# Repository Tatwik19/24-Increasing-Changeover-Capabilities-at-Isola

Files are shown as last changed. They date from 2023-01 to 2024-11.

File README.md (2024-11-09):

# 24-Increasing-Changeover-Capabilities-at-Isola
Innovation showcase poster pptx

<br />

https://github.com/user-attachments/assets/ee0afaa7-376b-4424-b353-ba5e18c106c2

<br />

The Isola Group is a global company that services the manufacturing industry by producing and supplying a range of products and raw materials. Their Chandler plant is designed specifically to produce copper-fiberglass laminate for PCBs, with a focus on high-speed turnaround low-volume custom substrate. Isola has identified the current copper foil roll changeover solution on their assembly line as a bottleneck. It is currently a slow, partially manual process, and speeding up this portion of the assembly line would allow them to take on more next-day clients, fill more orders, and generate more value. Team 24 has been tasked with designing a solution that can decrease the copper foil changeover time and remove the bottleneck in their line. The deliverables consist of a detailed mechanical and electrical design, a bill of materials (BOM) of the completed solution, and a budget for a completed solution. The solution’s scope is limited to the beginning of the process at the copper foil pallet staged at the machine and ending with loading the copper foil rolls onto the existing chucks.

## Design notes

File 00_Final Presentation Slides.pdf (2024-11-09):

# Final Presentation Team 24

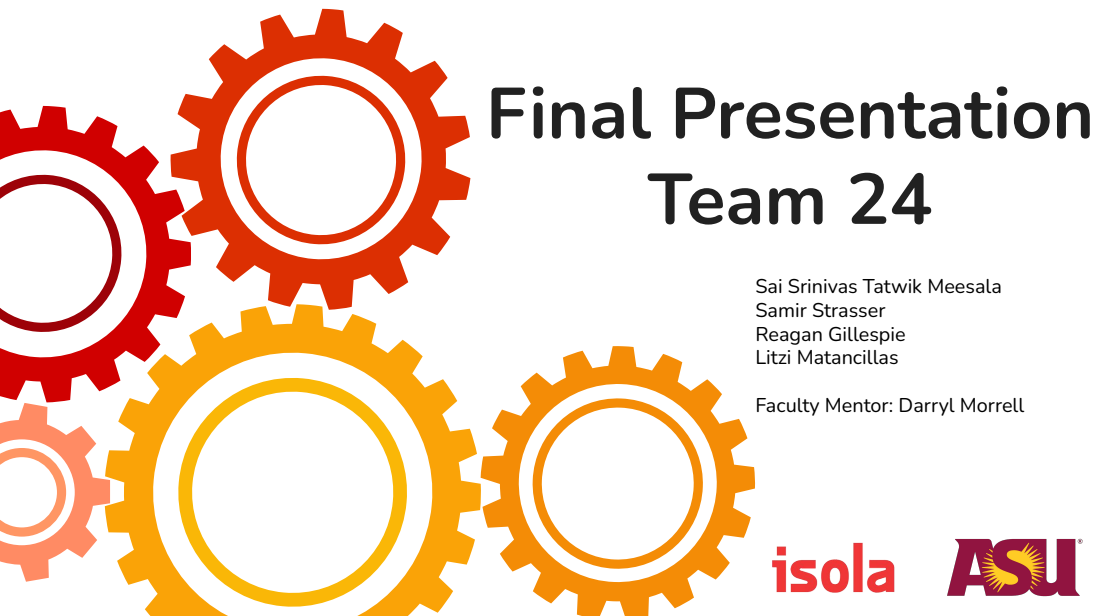
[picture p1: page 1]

Sai Srinivas Tatwik Meesala
Samir Strasser
Reagan Gillespie
Litzi Matancillas
Faculty Mentor: Darryl Morrell

# Problem Statement

## Isola's current copper foil roll changeover solution is largely a

manual process and takes 2 min which is far longer than it should,

## decreasing their ability to fill out next-day Printed Circuit Board

(PCB) orders. Along with that it currently can only hold 2 rolls,

## because of this it has become a bottleneck in the PCB material

production line.

# Concept: Dual Head Lifter

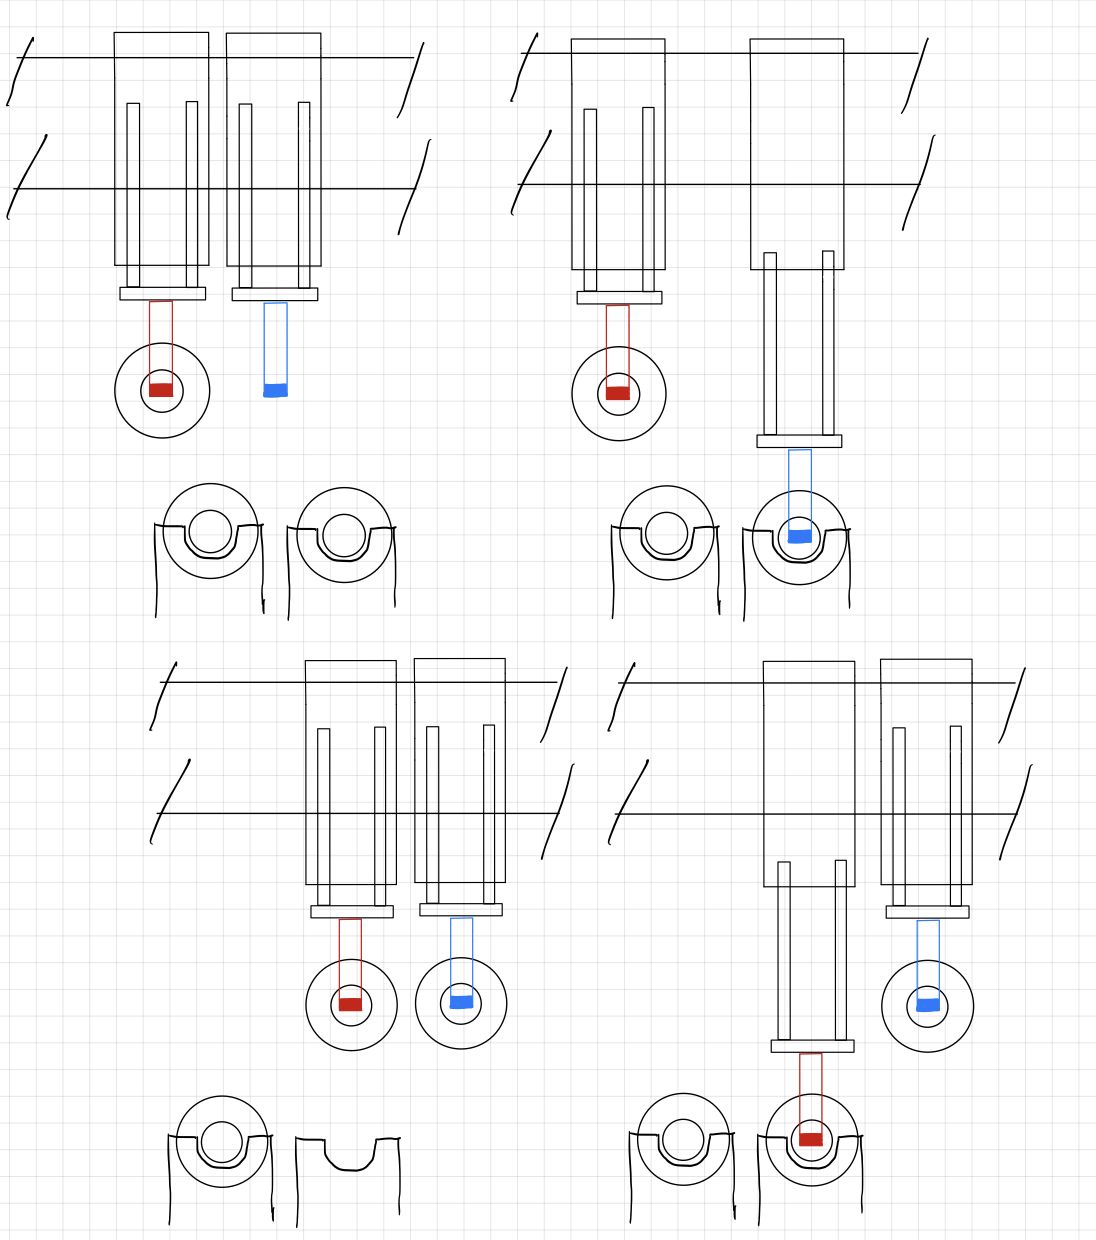
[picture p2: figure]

The automated hoist system features two independently driven cranes designed to efficiently replace copper rolls. The system utilizes two lifters, each capable of holding a roll, for quicker and smoother roll changes. With the ability to pick up and deposit rolls without damaging the copper, the machine reduces stress on the operator, making it a highly effective and reliable solution for automated or semi-automated roll replacement.

Pros | Cons
- Holds 2 rolls ● Can be attached to existing gantry ● Allows rolls to be picked up and dropped simultaneously, speeding up changeover time ● All loads are vertical | ● May not fit on the existing gantry ● Requires a second drive system ● May be expensive

# Full Assembly

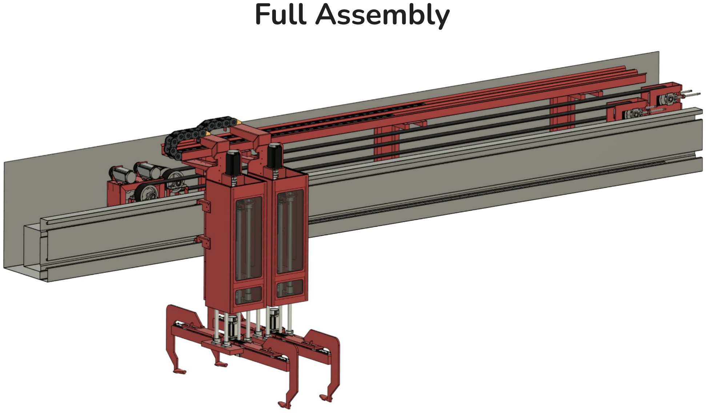
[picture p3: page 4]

# Detailed View Full Assembly

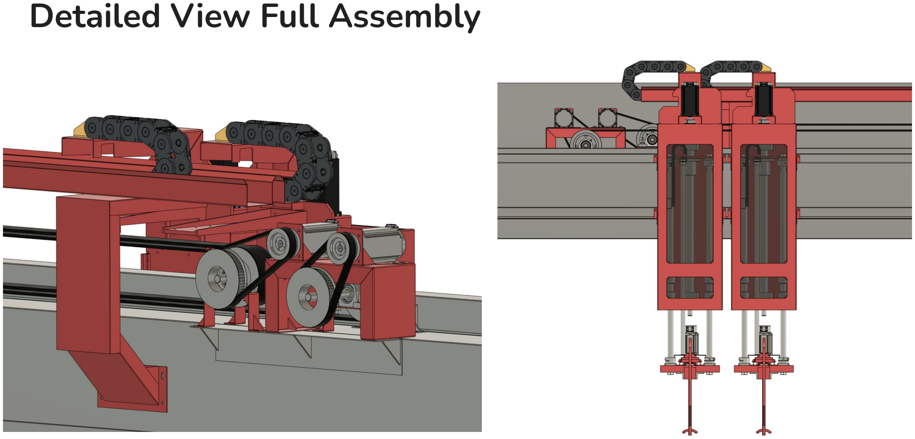
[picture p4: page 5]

# Detailed View Full Assembly

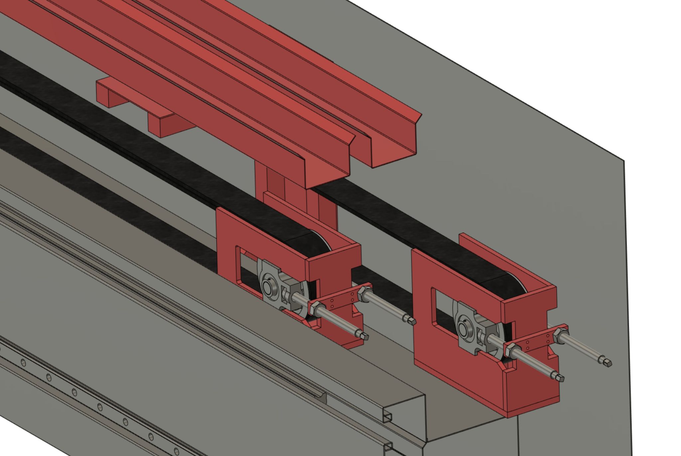
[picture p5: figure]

# Detailed View Full Assembly

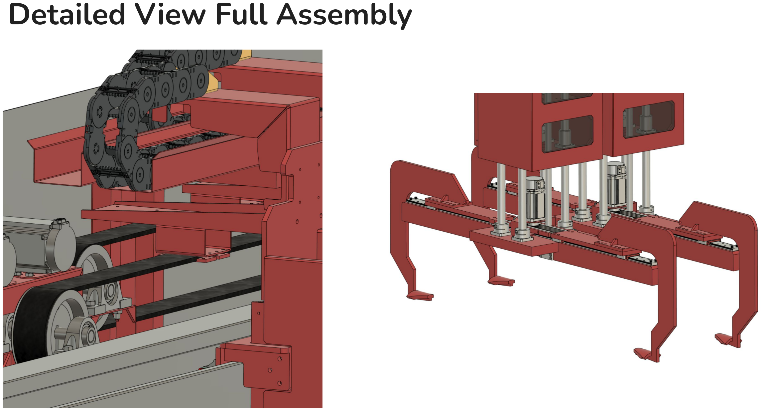
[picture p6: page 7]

# Detailed View Full Assembly

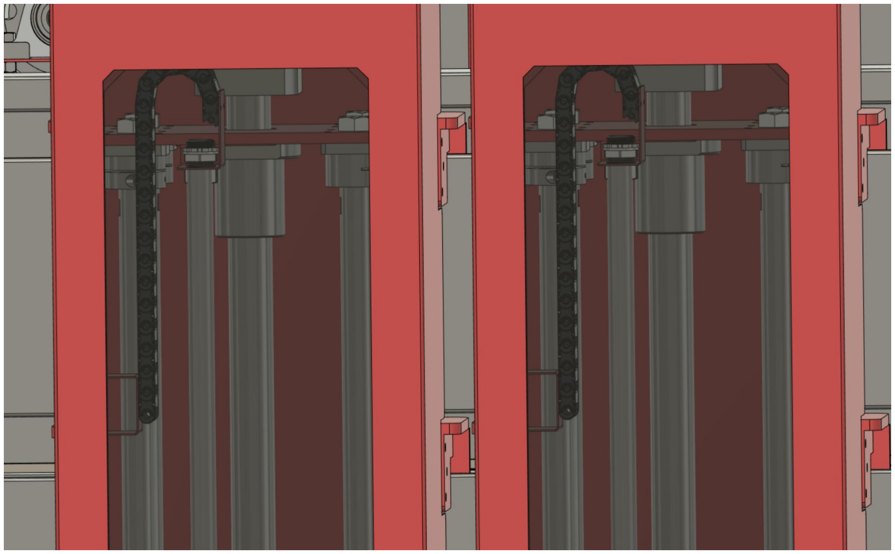
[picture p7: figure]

# Detailed View Full Assembly

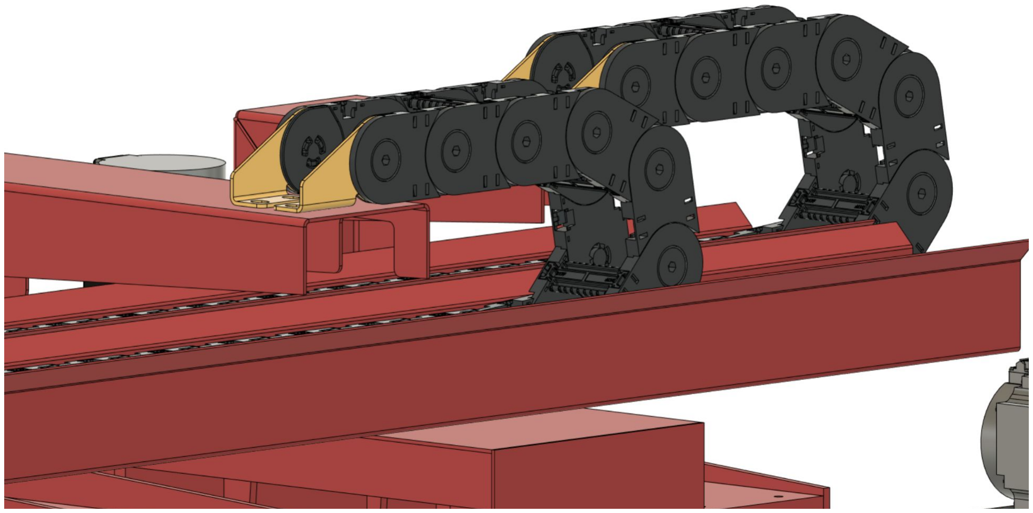
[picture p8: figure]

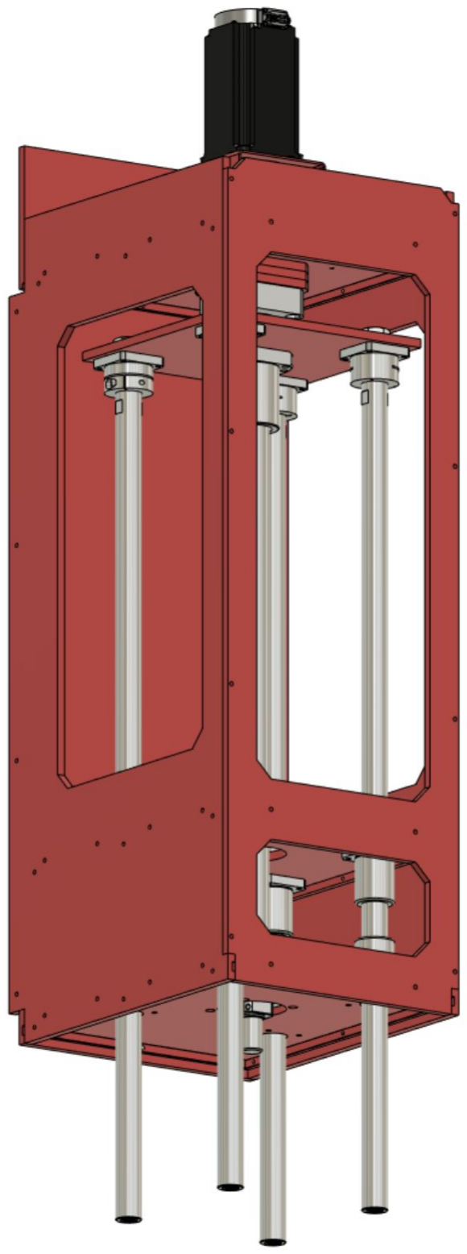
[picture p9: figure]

## - System uses a ball screw driven by a Mitsubishi servo motor - Uses four 30mm hollow stainless steel linear shafts to connect to the Y-axis - Frame is made of welded 10mm stainless steel plate. Laser cut with machined straight grooves for

alignment.

# CAD Model of Z-Axis

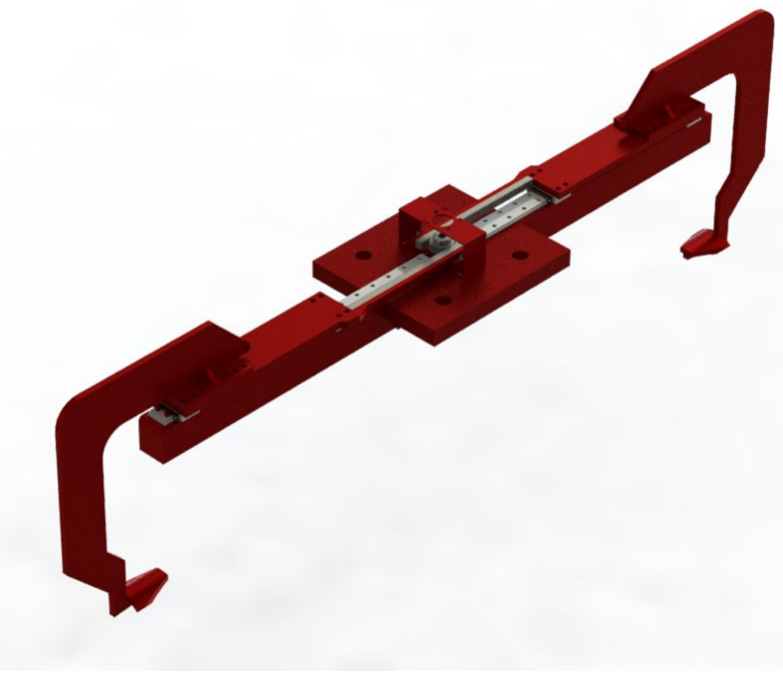
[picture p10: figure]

## - System uses a rack and pinion along with linear rails to move the end effector - The Y axis is moved up and down by the Z axis design - Weight: ~230 lbs - Whole design is made out of stainless steel

# CAD Model of Y-Axis

# CAD Model of Y-Axis

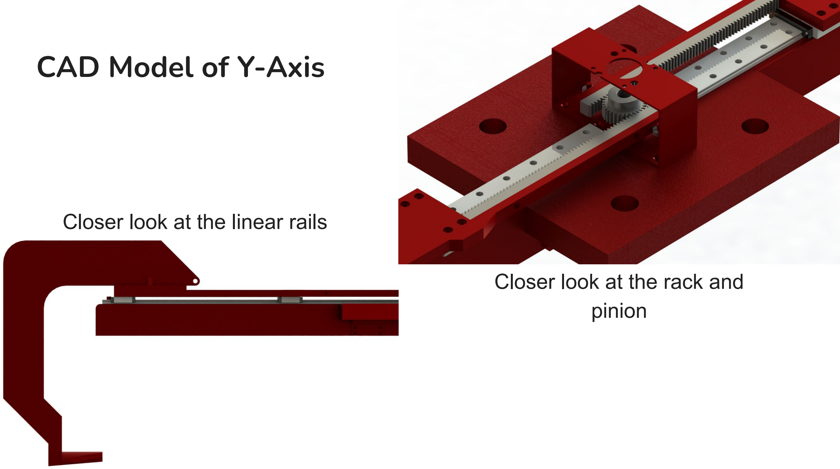
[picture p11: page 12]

## Closer look at the linear rails

## Closer look at the rack and pinion

# CAD Model of X-Axis

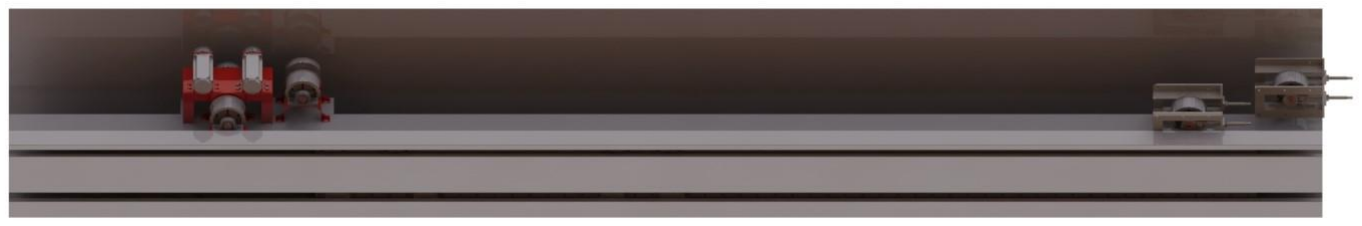
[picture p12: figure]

# CAD Model of X-Axis

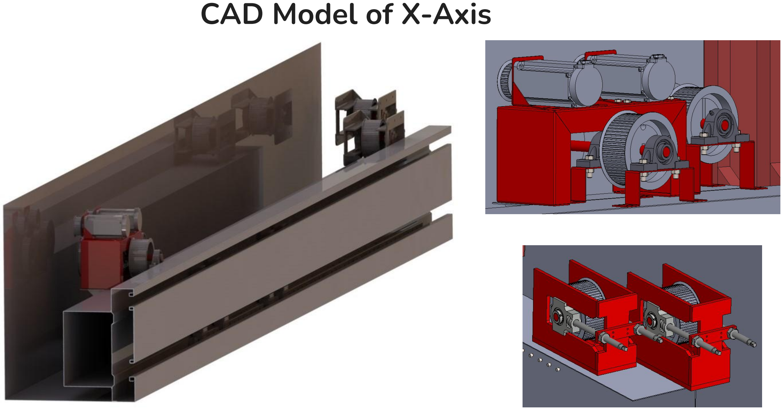
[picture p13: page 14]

# CAD Model of X-Axis

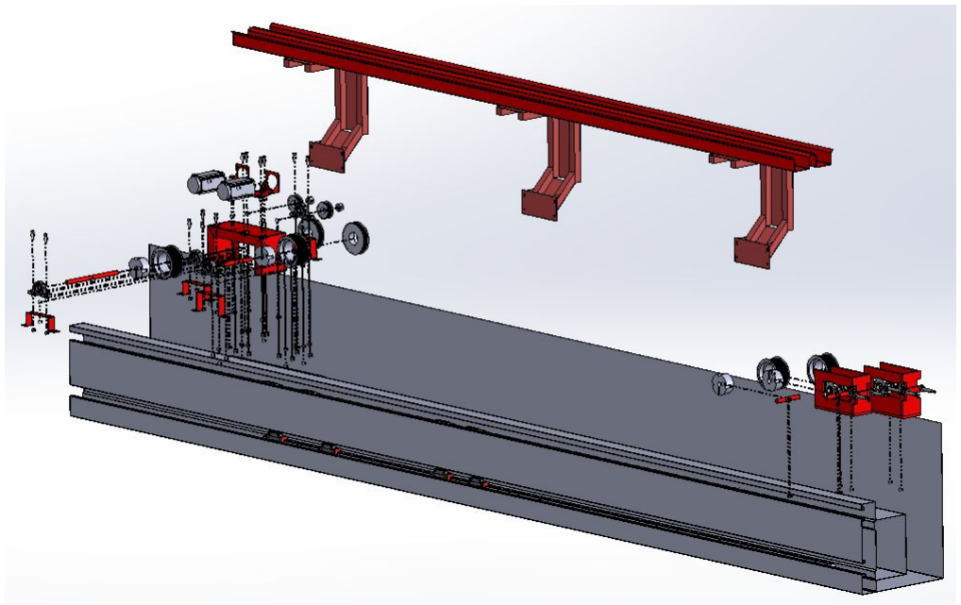
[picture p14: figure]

# Electrical schematic

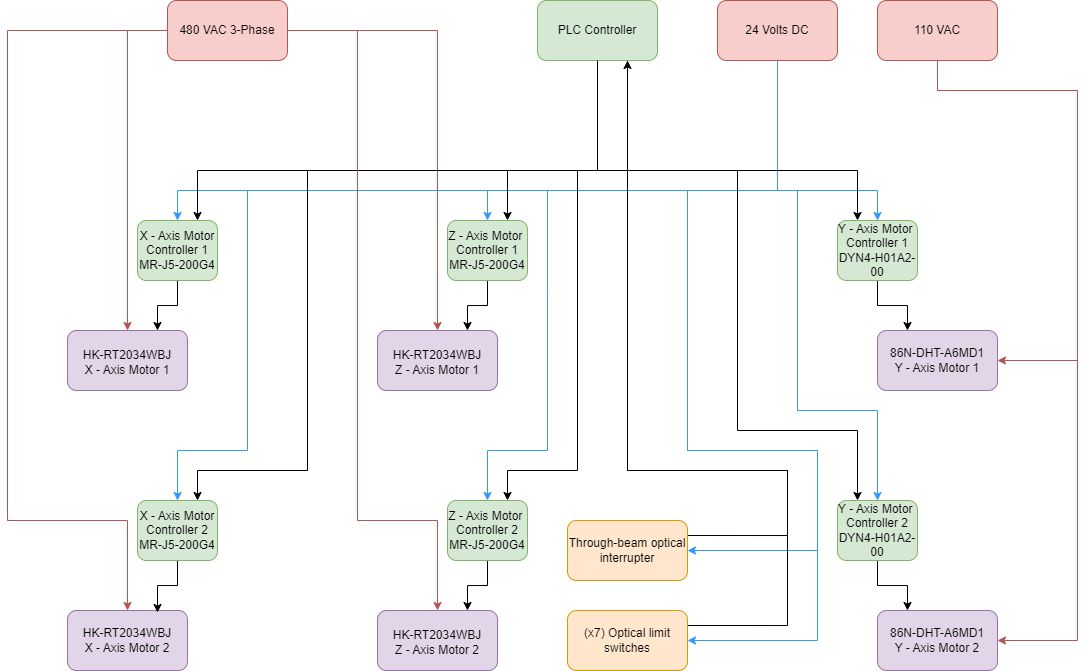
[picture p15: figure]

# Control flow schematic

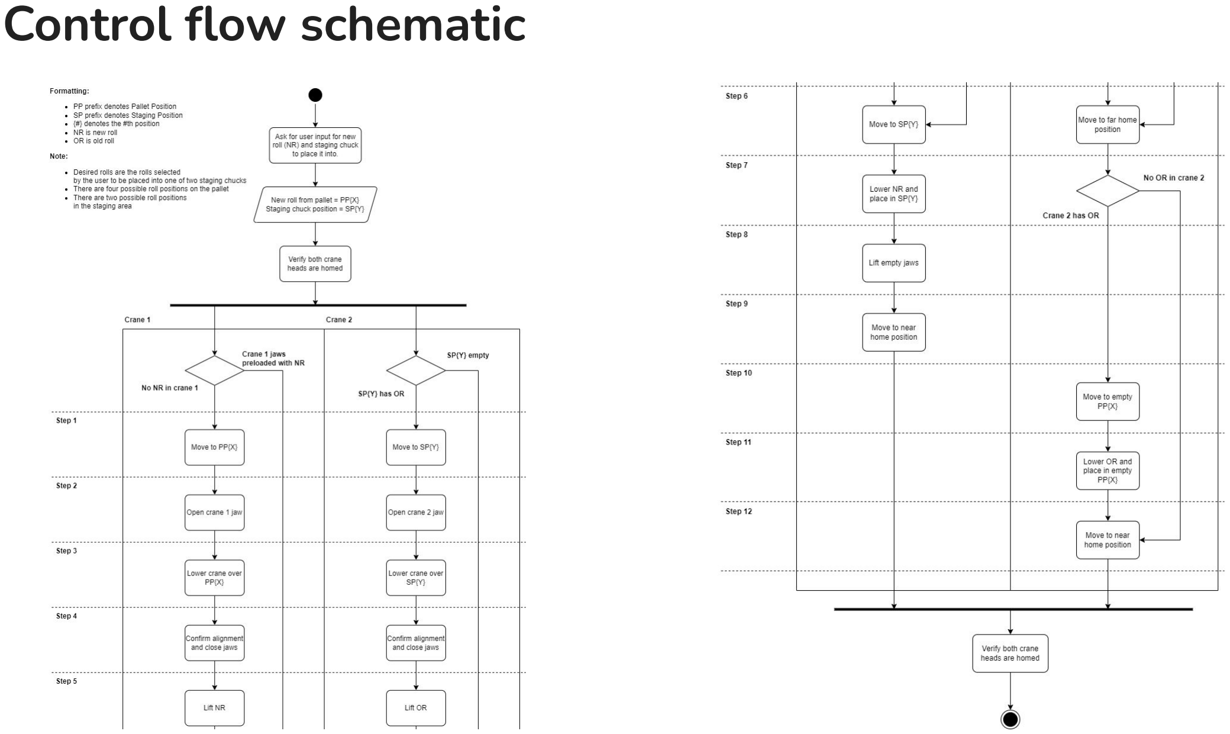
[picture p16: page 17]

# Control flow example

| Crane 1 | Crane 2
1 | Move from home to pallet position 1 | Move from home to staged position 2
2 | Open crane 1 jaws | Open crane 2 jaws
3 | Lower crane 1 over pallet roll 1 | Lower crane 2 over staged roll 2
4 | Confirm alignment and close jaws | Confirm alignment and close jaws
5 | Lift pallet roll 1 | Lift staged roll 2
6 | Move from pallet position 1 to staged position 2 | Move from staged position 2 to far home position
7 | Lower pallet roll 1 and place in staging chuck 2 | Wait for crane 1 step 7 to complete
8 | Lift empty crane 1 head | Wait for crane 1 step 8 to complete
9 | Move to near home position | Move to empty pallet roll 1 position.
10 | Wait at near home position | Lower staged roll 2 and place in empty pallet roll 1 position
11 | Wait at near home position | Lift empty crane 2 head
12 | Wait at near home position | Move to near home position

# Success Criteria that were tested

# Changeover Time

1. Generate simplified CAD design 2. Create analytical model of system in MATLAB 3. Simulate a set of roll changeover scenarios with Simulink 4. Determine the changeover time with the CAD specifications 5. Evaluate results, determine if success criteria are met, and decide how to iterate on initial design

# Weight Capacity

### 1. Isolate the affected parts of assembly 2. Run static FEA a. Define Fixture and load locations 3. If passed, run dynamic FEA 4. Evaluate results a. Determine if success criteria are met b. Decide how to iterate on initial design

# Timing analysis results - Simulation in Simulink

### Steps for Worst Case scenario

### 1: Move Z - Axis Down no roll14 in (0.3556m) -

### 2: Move Y - Axis in -

### 3: Move Z - Axis Up with roll 14in (0.3556m) -

### 4: Move X - Axis 3.7m -

### 5: Move Z - Axis down with roll -

### 6: Move Y - Axis out -

### 7: Move Z - Axis up no roll -

### Time

1: 1.5 s

2: 2 s

3: 5 s

4: 20 s

5: 4.5 s

6: 2 s

7: 1.5 s

### Total = 36 s

# Z-axis Weight Capacity Analysis - Solidworks Simulations

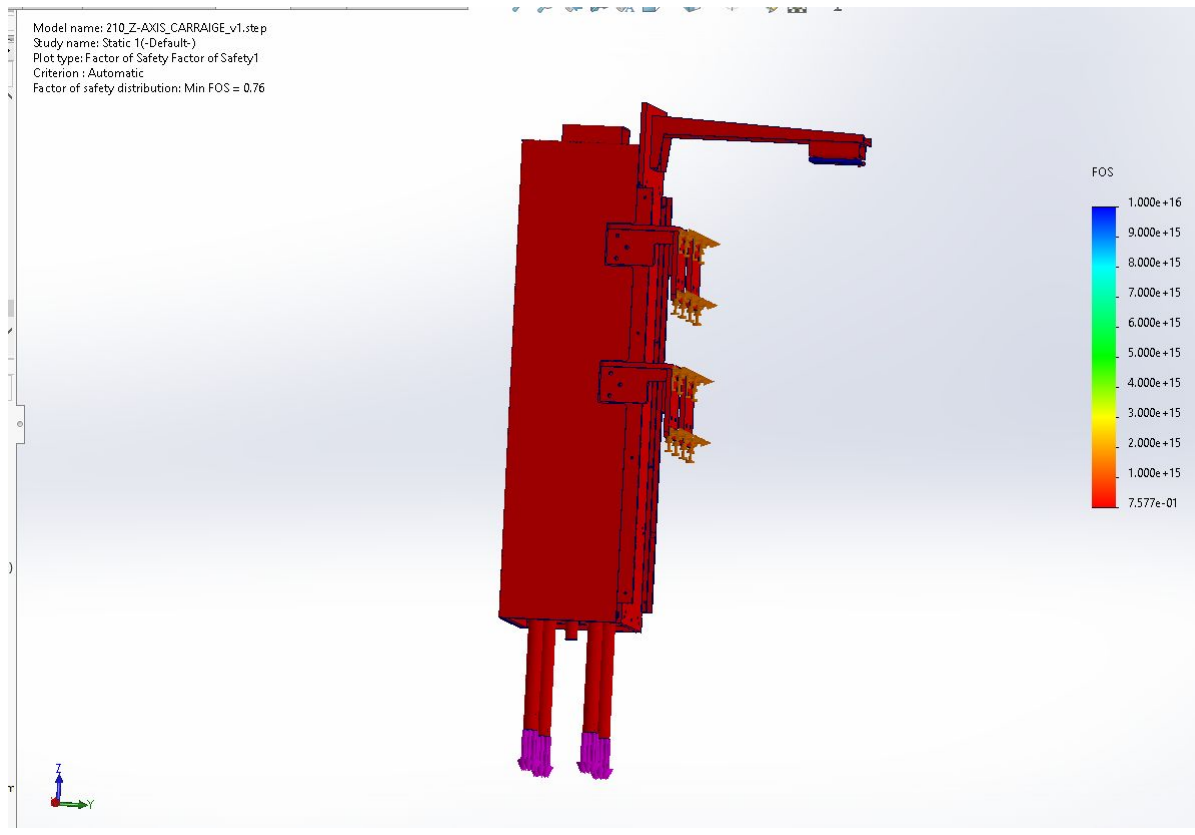
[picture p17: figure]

## - FOS of .76 with 1300 lbf

- 1000lbs for copper roll
- 300lbs for y-axis

## - CAD software

- Fusion 360

## - Stress Report

- https://docs.google.com/document/d/1KZtIbDu

P4CQBt1wj39I0JRIAjMUCrfVk/edit?usp=sharin g&ouid=117687347861756154722&rtpof=true &sd=true (https://docs.google.com/document/d/1KZtIbDuP4CQBt1wj39I0JRIAjMUCrfVk/edit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)

# Y-axis Weight Capacity Analysis - Solidworks Simulations

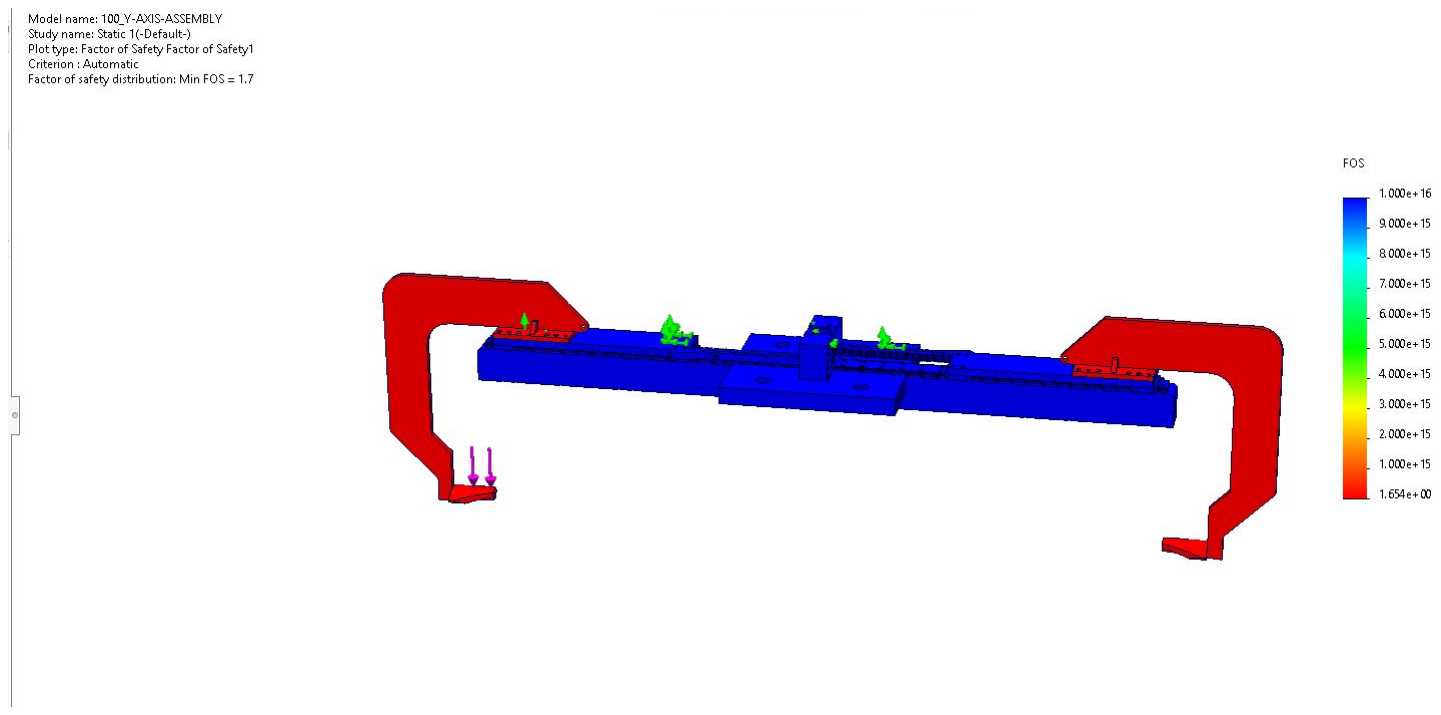
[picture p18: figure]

## - FOS of 1.7 with 1000 lbf - CAD software

- Solidworks

## - Stress Report

- https://docs.google.com/document/d/1j

Z49amwHMNin8M4D6h1QPXJ2rFmE6 KR2/edit?usp=sharing&ouid=11768734 7861756154722&rtpof=true&sd=true (https://docs.google.com/document/d/1jZ49amwHMNin8M4D6h1QPXJ2rFmE6KR2/edit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)

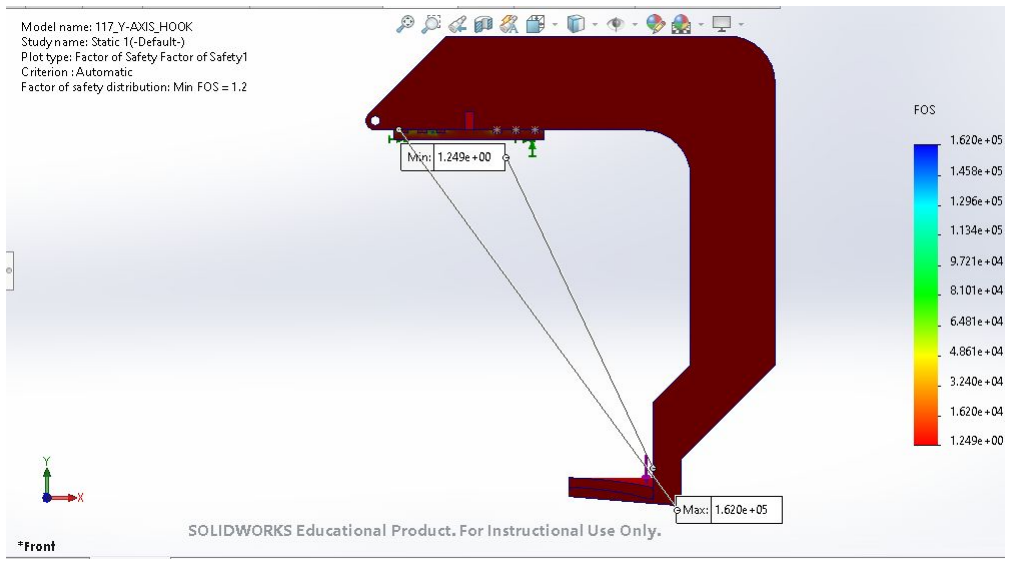
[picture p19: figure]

## - 1000 lbf downwards on where the copper roll would be place - Safety factor of 1.2

- Can hold max of 1200 lbf

# CAD Model of End Effector

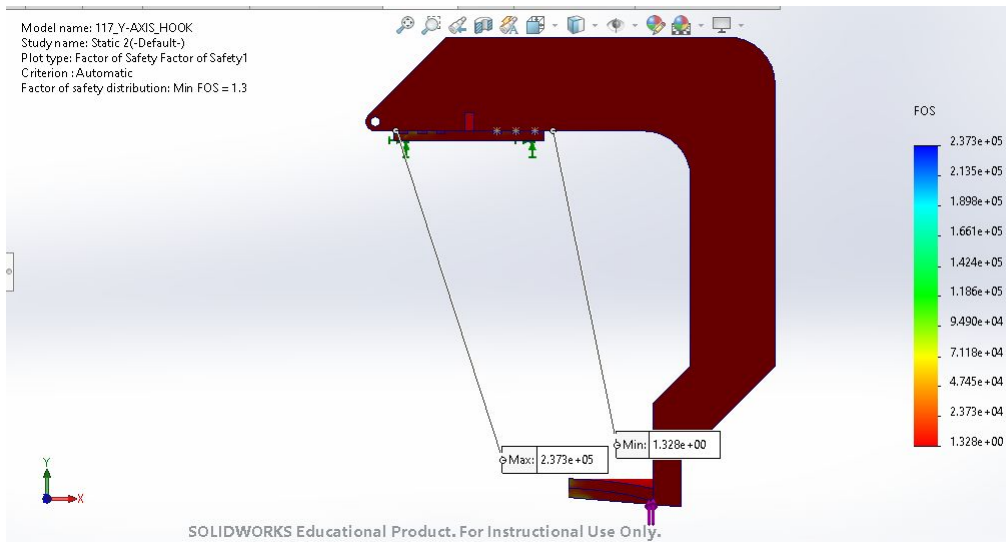
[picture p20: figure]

## - 626 N + 100 N applied sideways to simulate fast acceleration - Safety factor of 1.3

- Can withstand
acceleration up to 943 N

# CAD Model of End Effector

## - Device should follow the following OSHA standards: 1910, 1926, 1809 - Device should follow Class 6 clean room standards - Device should interface with Mitsubishi PLC control systems by following IEC

61131-3
- Device should be built using ISO 724 Metric threaded hardware.

# Project Success Criteria

Criterion (Requirement) | Threshold (Halt & Review) | Team’s concept | POR Risk (H, M, L) | Comments
Number of rolls staged on machine | 4 | 5 | L | The dual hoist system adds extra roll space
Changeover time | 40 sec | 36 sec (worse case scenario) | M | Even at worst case scenario team is able to keep the change over time under 40 sec.
Per roll weight capacity | 500 lb | 750 lbs | L | Controllable by design
Clean room standard | Class 6 | Class 6 | L | The components used in the design rated to maintain air cleanliness levels of a maximum of 1,000 particles per cubic meter

# Video demonstration of Project

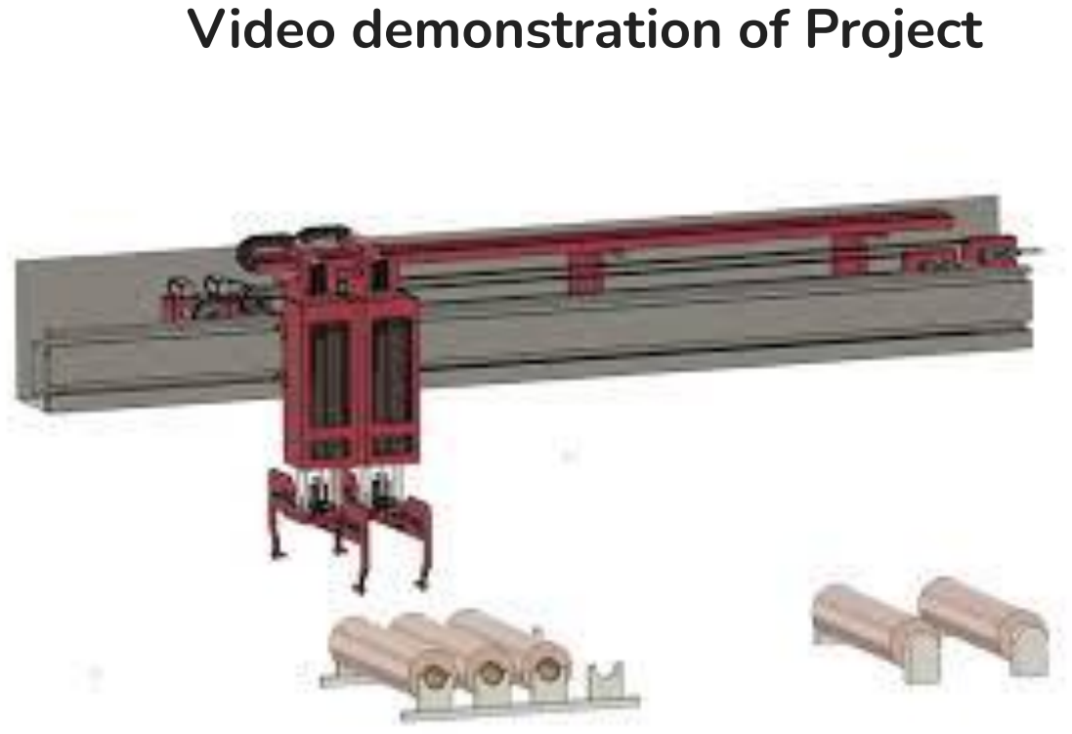
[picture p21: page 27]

# BOM

X axis (horizontal)
x drive motor | HK-RT2034WBJ | Mitsubishi | | Link (https://www.mitsubishielectric.com/fa/download/cad/index.html)
x drive motor driver | MR-J5-200G4 | Mitsubishi
x drive main pulley | 8MX-60S-62 | Gates Corp | $ 500.00 | Link
x drive main pulley bushing | 3020 24MM 7859-6524 | Gates Corp | $ 50.50 | Link (https://www.royalsupply.com/store/pc/Gates-3020-24MM-3020-TL-Bushing-24mm-Bore-7859-6524-5825p67592.htm)
x drive Idler pulley bushing | Gates 3020 25MM Bushing | Gates Corp | | Link
x drive Idler pulley tensioner | TUUFLN25 | Misumi | $ 100.00 | Link (https://us.misumi-ec.com/vona2/detail/110310287189/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)
x drive motor pulley | 8MX-30S-21 | Gates Corp | $ 200.00 | Link
x drive motor pulley bushing | 1108/19mm 7858-0119 | Gates Corp | $ 30.00 | Link (https://www.royalsupply.com/store/pc/Gates-1108-19MM-1108-TL-Bushing-19mm-Bore-7858-0119-p67533.htm)
x drive drive pulley | 8MX-60S-21 | Gates Corp | $ 200.00 | Link
x drive drive pulley bushing | 2012 24MM 7858-2524 | Gates Corp | $ 30.00 | Link (https://www.royalsupply.com/store/pc/Gates-2012-24MM-2012-TL-Bushing-24mm-Bore-7858-2524-5824p67564.htm)
x axis pillow block bearing | Ultra Class Series UCP - Pillow Block - Wide
x drive belt | LL8MGT-036 (inquire abt 62) | Gates Corp | $ 100.00 | Link
x reducer belt | 8MGT-1120 P.L. 44.09 140 Teeth | Gates Corp | $ 100.00 | Link
x axis linear rail | HGW35CA2R3700ZBCII | HIWIN | - | Link
x optical limit switches | PR-F51CP | Keyence | $ 150.00 | Link (https://www.keyence.com/products/sensor/photoelectric/pr-m_f/get-pricing/?model=pr-f51cp)
Inner Ring, Set Screw (UCP-7/8) | Misumi | $ 80.00 | Link (https://us.misumi-ec.com/vona2/detail/221303354946/?HissuCode=UCP-7%2F8)

# BOM

Z axis (lift)
z drive motor | HK-RT2034W | Mitsubishi | $ 2,000.00 | Link
z ball screw | RBS-R40-10T4-FSI-600-822-0.05-M | Hiwin | - | Link
z linear shaft | SSPJ30-1000 | Misumi | $ 894.80 | Link
z linear shaft bearings | LMK30MUU | Misumi | $ 227.00 | Link
z linear shaft mounts | SSTHWS30b | Misumi | $ 150.00 | Link
z drive coupling | SCXW55-19-25 | Misumi | $ 50.00 | Link
z limit switches | PR-M51CP | Keyence | $ 150.00 | Link
z ball screw supports | FK-30B | Hiwin | $ 300.00 | Link
z locating pins | AJPNGB5-P6-B8-G5-RAC | Misumi | $ 5.48 | Link

# BOM

Y axis (end effector)
y actuation motor | 86N-DHT-A6MD1 | Dynamic Motor Motion | $ 292.00 | Link (https://teknic.com/model-info/CPM-MCPV-2311D-RLN/?model_voltage=75VDC)
y motor driver | DYN4-H01A2-00 | Dynamic Motor Motion | $ 235.00
y Pinion | GEAS1.5-30-15-B-13 | Misumi | $ 45.00 | Link (https://us.misumi-ec.com/vona2/detail/110300428520/?Tab=preview)
y Rack | RGEAS1.5-300-Z | Misumi | $ 186.00 | Link (https://us.misumi-ec.com/vona2/detail/110300429830/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)
y linear rail | SSE2BWML16G-669 | Misumi | $ 543.00 | Link (https://us.misumi-ec.com/vona2/detail/110300046230/?Tab=preview)
y through beam | PR-G51CP | Keyence | $ 150.00 | Link
y limit switches | KSK6-AP-4H | Automation Direct | $ 35.00 | Link
y limit switch bracket | ST18C7W | Automation Direct | $ 7.25 | Link
Total | | | $6,779

# Management: Risks

Risk Number | Triggered (Y/N) | Description of Risk | Owner/ Responsible | Type | Severity (H/M/L) | Mitigation Strategy | Actions to Mitigate
R2 | N | Our industrial partner may not be able to meet on a regular schedule since he is the Plant Engineering Manager | Team | Commun ication | M | Address | We will talk to our industry partner about meeting at different times

R3 | N | The team may not be able to properly model the full-scale system with a smaller scale prototype, leading to uncertainties in the design. | Team | Technical | L | Address | We will ask for assistance from our IP or from our mentors
R4 | N | The team cannot test if the solution will have a 20 year lifespan, only make estimates and design in safety factors, so it is possible that the final solution may not last that long. | Team | Technical | M | Address | We will ask for assistance from our IP or from our mentors
R5 | N | The Return on Investment (ROI) of the project may not be under 2 years if the final solution is too expensive | Team | Financial | H | Address | We will talk to the IP and see if there is anything we can do

# Evaluation of Planned vs Actual schedule

## - The only time we fell behind schedule was completing the BOM

- This happened because we had to change parts out a few times (mainly the Y axis motor and sensors)

## - Overall we met our schedule for every big milestone

Milestone | Due Date
Design Review | Oct 31st
Preliminary Prototype Plan | Nov 2nd
Sourcing Parts both electrical and mechanical | Feb 5th

Initial Prototype Complete (CAD model and Analysis) & Design
Review

Jan 23st

Second Design Review | Mar 5th
Final project delivery date | Apr 28th

Color Key

Completed on/before time

Was late less than one
week

Was late more than one
week

## - Our team fully designed a twin hoist system to accelerate the copper roll changeover process - Our team hit all of our success criteria and deliverable

# Conclusion

## - The control of the axis (the PID’s) can be further optimized using Mitsubishi’s

built in PID tuning.

- This could further improve the timing of the system

## - Modify model to increase the FOS of the Z-axis to at least 1

- May have to modify the bracket

## - We made the assumption that the X-axis rails could hold the weight of the hoists (as we do not know the inside structure of the rails)

- New rails may have to be made to support the new weight

# Suggestions for future work

# Questions?

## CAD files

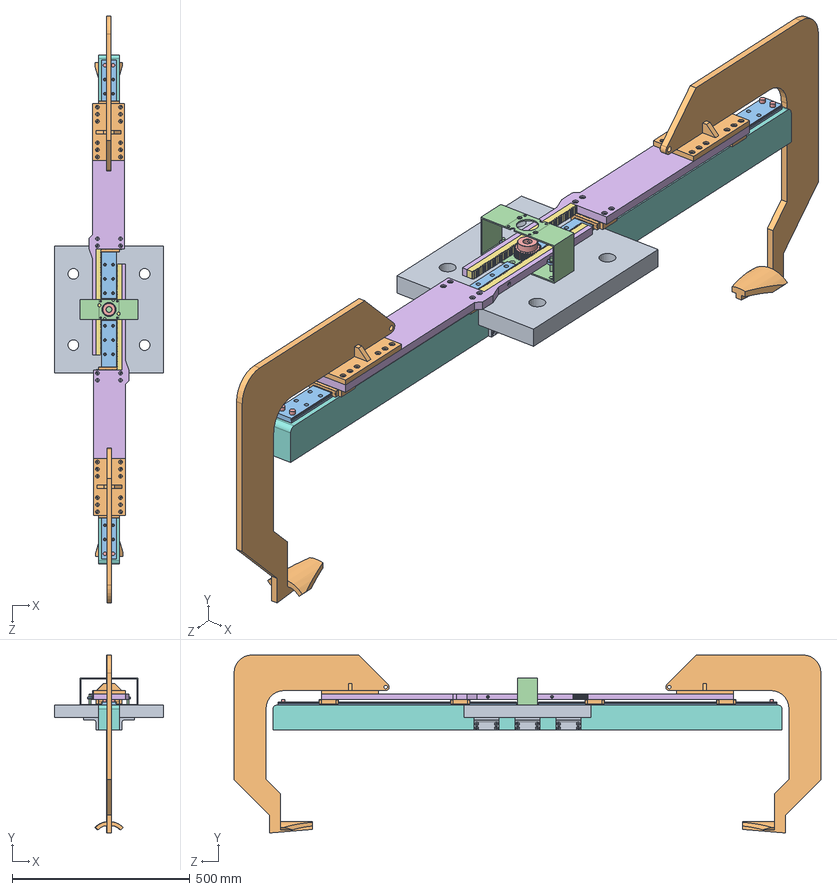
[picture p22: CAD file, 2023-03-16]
CAD/100_Y-AXIS-ASSEMBLY.SLDASM
304.8 x 500.0 x 1648.5 mm
121_Y-AXIS_BASE
131_Y_AXIS_LINEAR-RAIL_BASE x 4
132_Y-AXIS_LINEAR-RAIL_RAIL x 2
143_Y-AXIS-MOTORMOUNT
141_Y-AXIS_PINION
145_Y-AXIS_RACK-ATTACHMENT x 2
142-Y-AXIS-RACK_RGEAS1_5_300_A x 2
123_Y-AXIS-UNDER_BASE
122-Y-AXIS_L_BRACKET x 6
117_Y-AXIS_HOOK x 2
118_Y-AXIS_BEARING x 2
119_Y-AXIS-DOWEL x 2
1_1110_STOPPER x 4

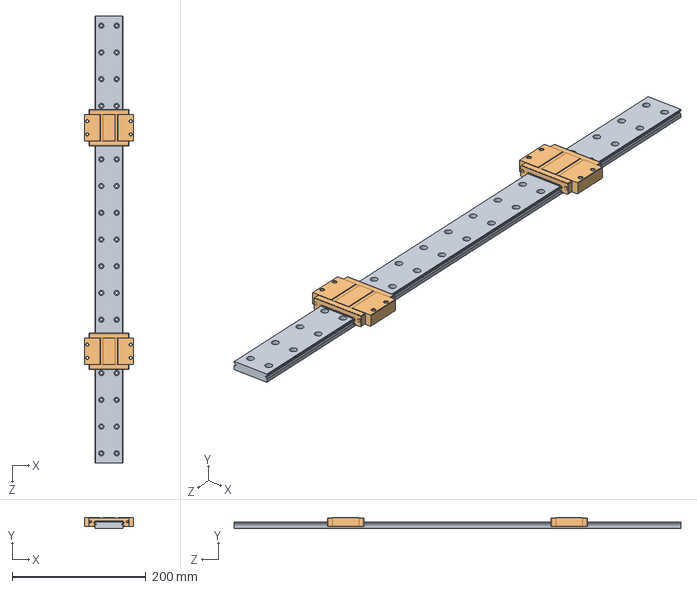
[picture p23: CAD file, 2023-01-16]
CAD/130-Y-AXIS_LINEAR-RAIL-ASSEMBLY.SLDASM
74.0 x 16.0 x 669.0 mm
132_Y-AXIS_LINEAR-RAIL_RAIL
131_Y_AXIS_LINEAR-RAIL_BASE x 2

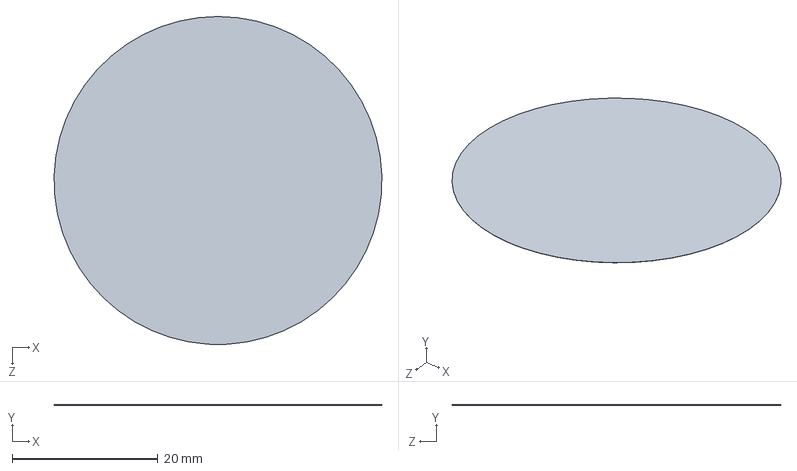
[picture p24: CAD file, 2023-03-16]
151_Y-AXIS_FORMATE.SLDPRT
45.0 x 0.0254 x 45.0 mm

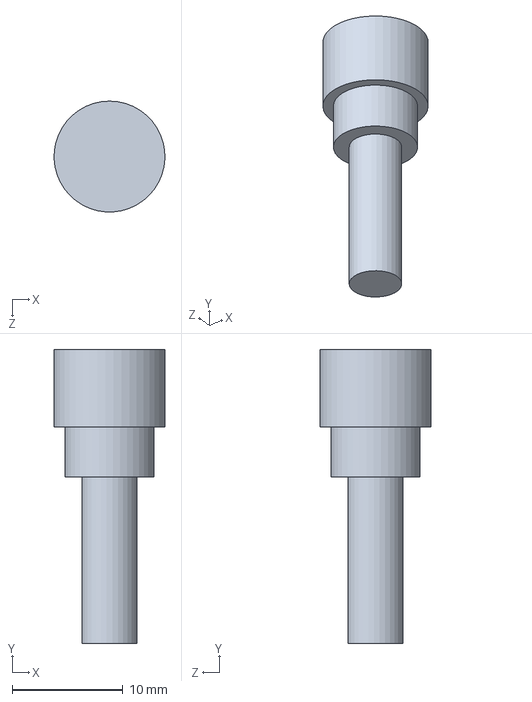
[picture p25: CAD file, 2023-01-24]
CAD/1_1110_STOPPER.SLDPRT
9.99 x 26.5 x 9.99 mm

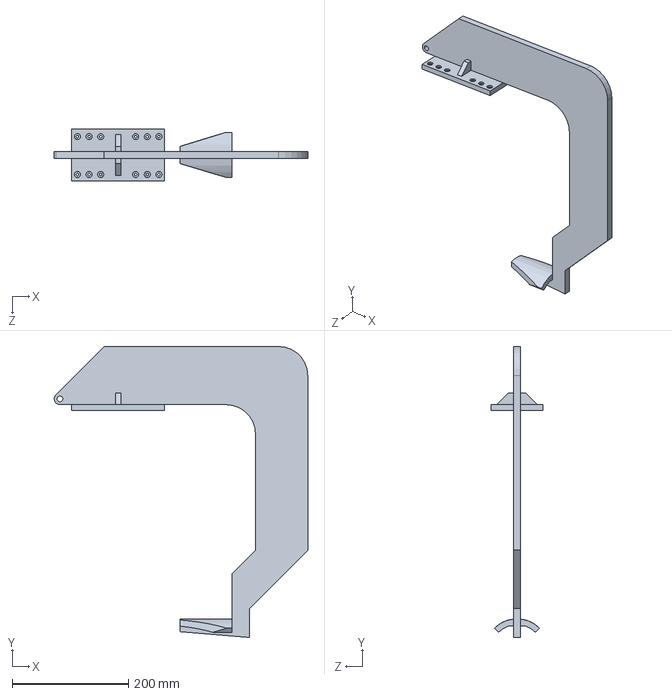
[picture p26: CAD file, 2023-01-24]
CAD/117_Y-AXIS_HOOK.SLDPRT
435.9 x 500.0 x 90.0 mm

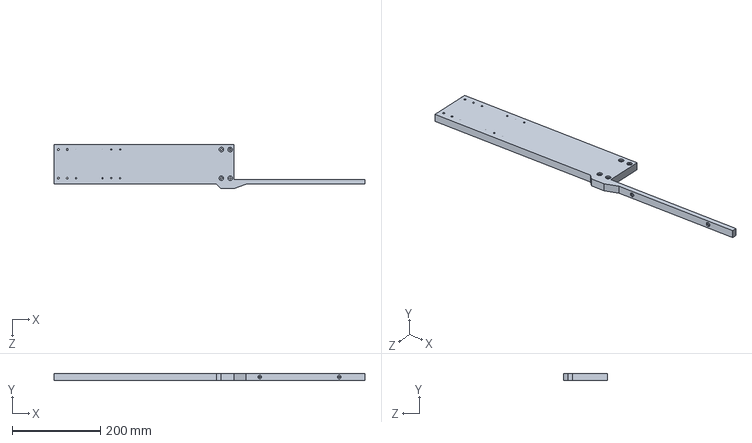
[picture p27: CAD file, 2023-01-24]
CAD/145_Y-AXIS_RACK-ATTACHMENT.SLDPRT
705.5 x 15.0 x 100.0 mm

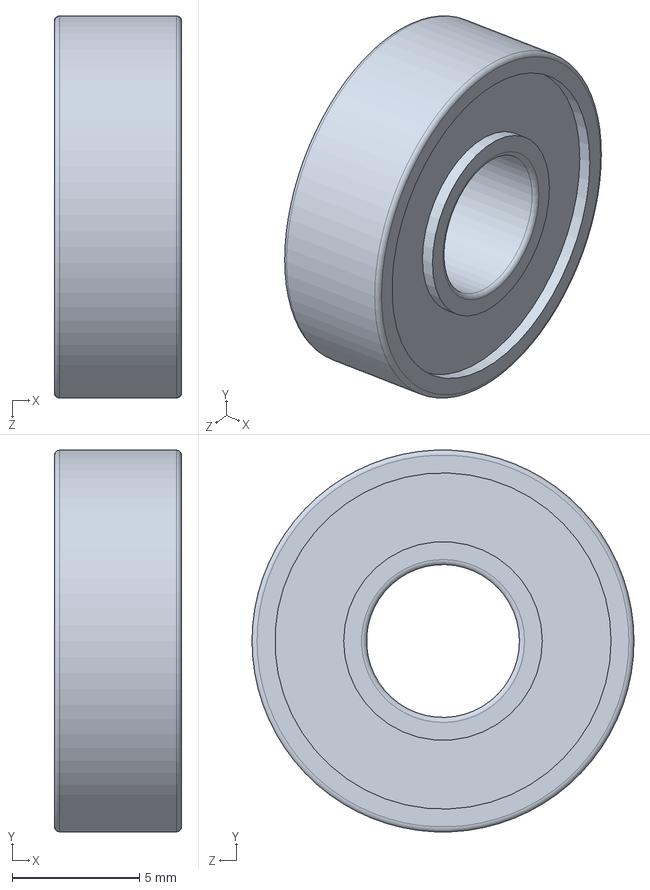
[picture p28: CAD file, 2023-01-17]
CAD/118_Y-AXIS_BEARING.SLDPRT
5.00 x 15.0 x 15.0 mm

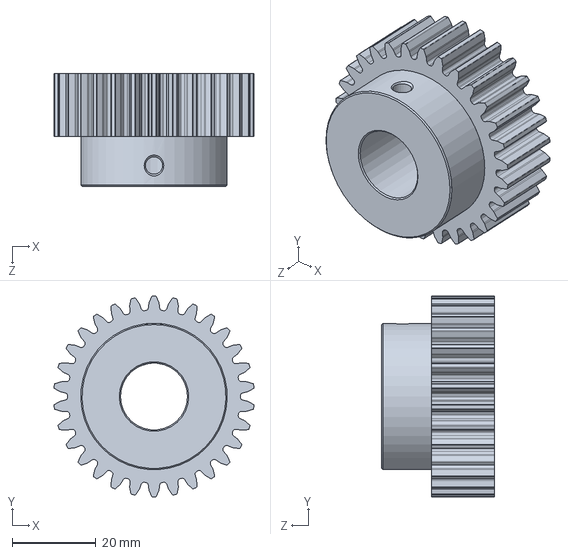
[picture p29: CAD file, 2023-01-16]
CAD/141_Y-AXIS_PINION.SLDPRT
47.8 x 48.0 x 27.0 mm

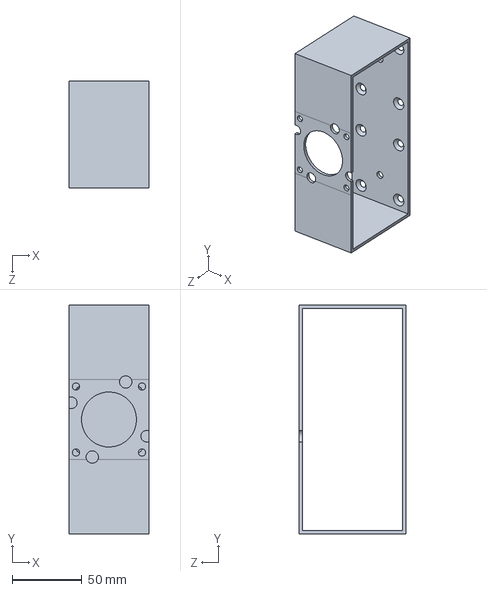
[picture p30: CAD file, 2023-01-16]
CAD/143_Y-AXIS-MOTORMOUNT.SLDPRT
57.0 x 163.6 x 76.2 mm

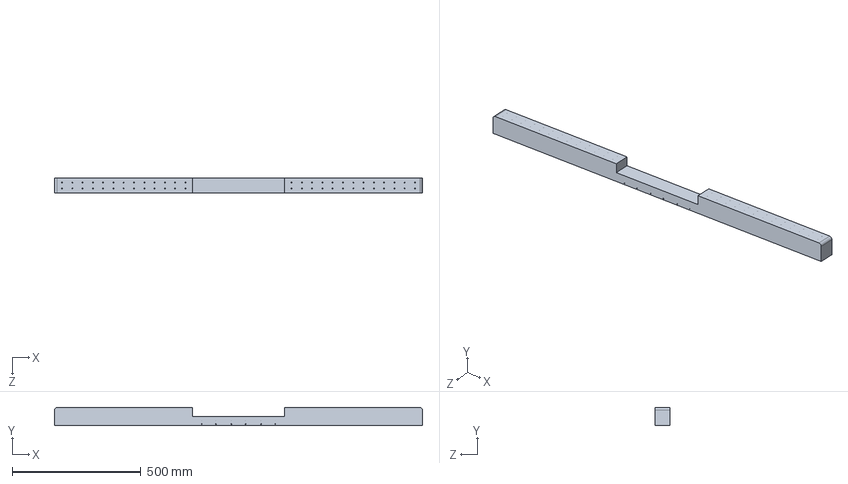
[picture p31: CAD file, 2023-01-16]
CAD/123_Y-AXIS-UNDER_BASE.SLDPRT
1430.0 x 70.0 x 60.0 mm

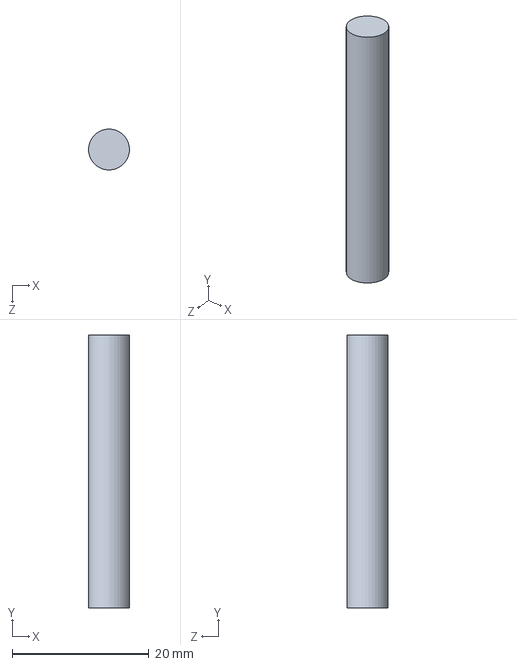
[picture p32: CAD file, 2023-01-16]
CAD/119_Y-AXIS-DOWEL.SLDPRT
5.99 x 40.0 x 6.00 mm

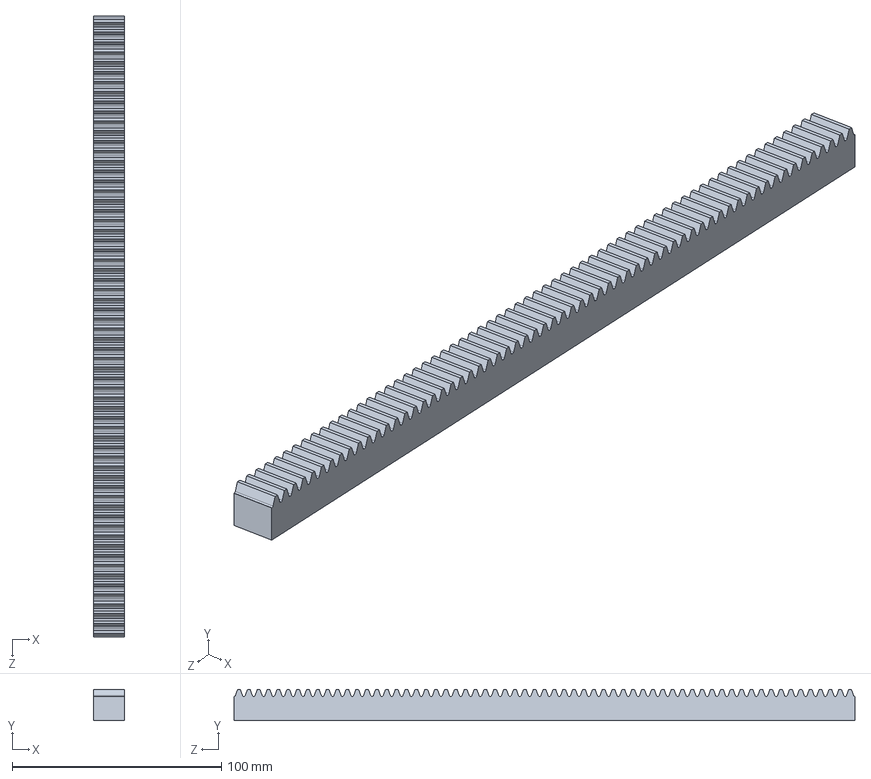
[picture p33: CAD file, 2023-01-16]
CAD/142-Y-AXIS-RACK_RGEAS1_5_300_A.SLDPRT
15.0 x 15.0 x 296.9 mm

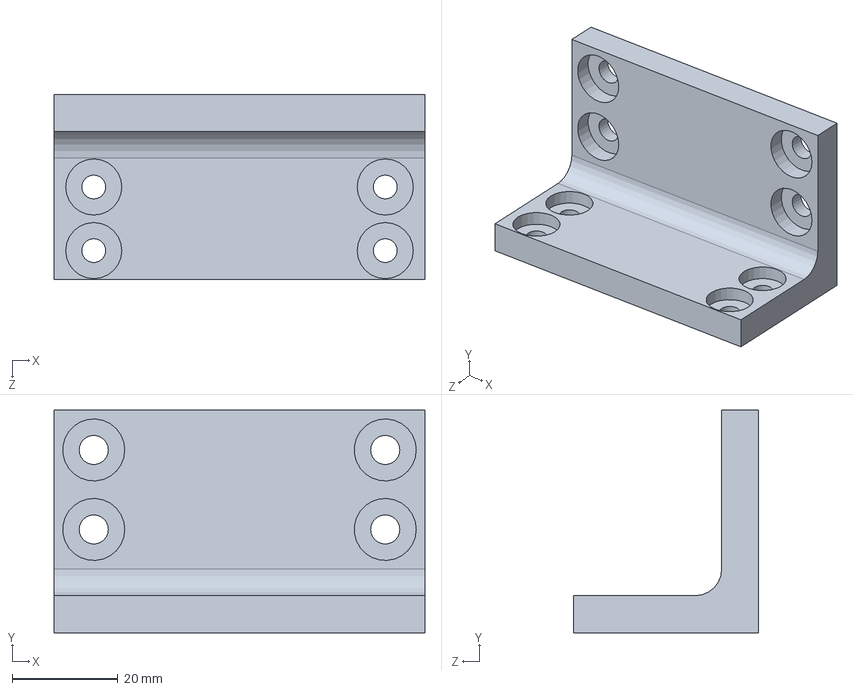
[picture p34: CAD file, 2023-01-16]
CAD/122-Y-AXIS_L_BRACKET.SLDPRT
70.0 x 42.0 x 35.0 mm

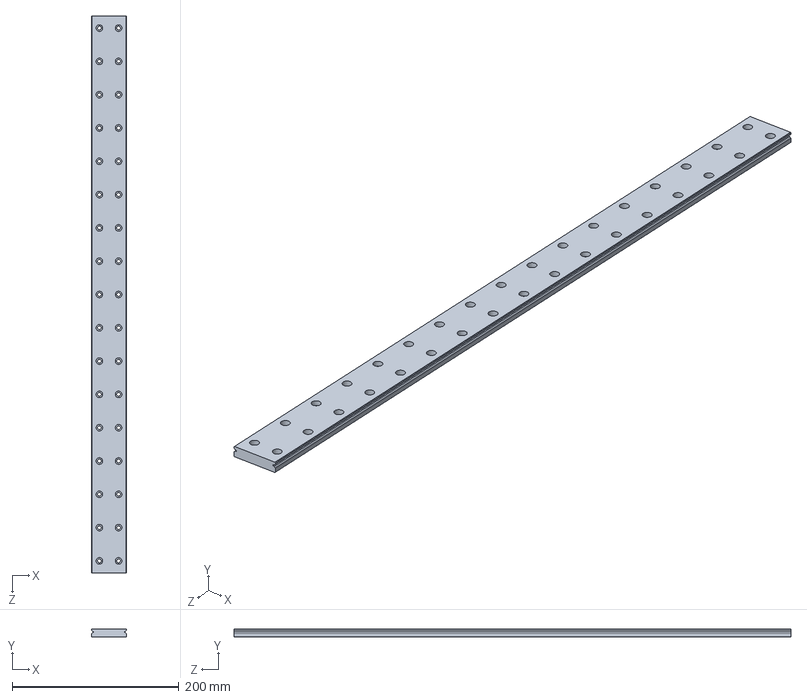
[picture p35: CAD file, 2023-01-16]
CAD/132_Y-AXIS_LINEAR-RAIL_RAIL.SLDPRT
42.0 x 9.50 x 669.0 mm

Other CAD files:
CAD/131_Y_AXIS_LINEAR-RAIL_BASE.SLDPRT
CAD/121_Y-AXIS_BASE.SLDPRT
CAD/ASU_A-size_Sht1_Metric (2).SLDDRW

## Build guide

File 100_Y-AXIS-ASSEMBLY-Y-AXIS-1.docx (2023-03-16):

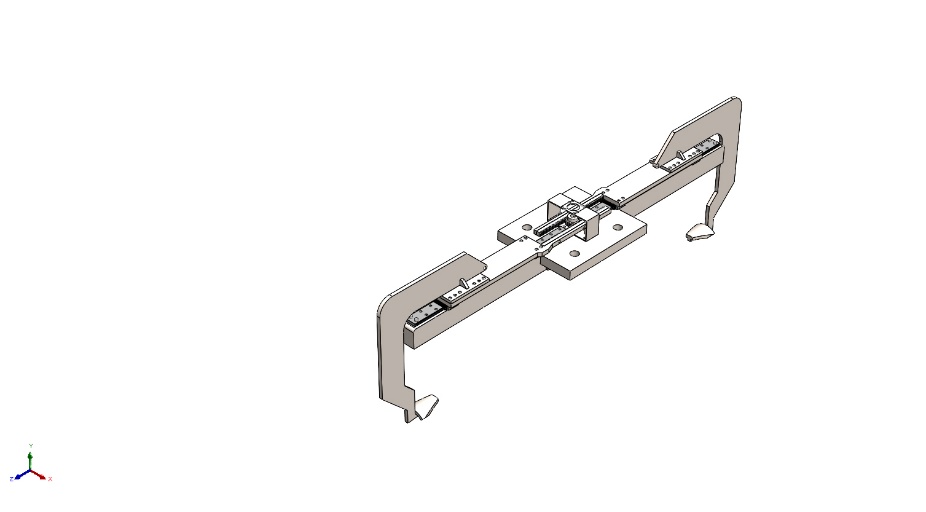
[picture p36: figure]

Simulation of 100_Y-AXIS-ASSEMBLY

Date: Thursday, 16 March, 2023
Designer: Solidworks

Study name: Y-AXIS

Analysis type: Static
Description No Data

# Assumptions

# Model Information

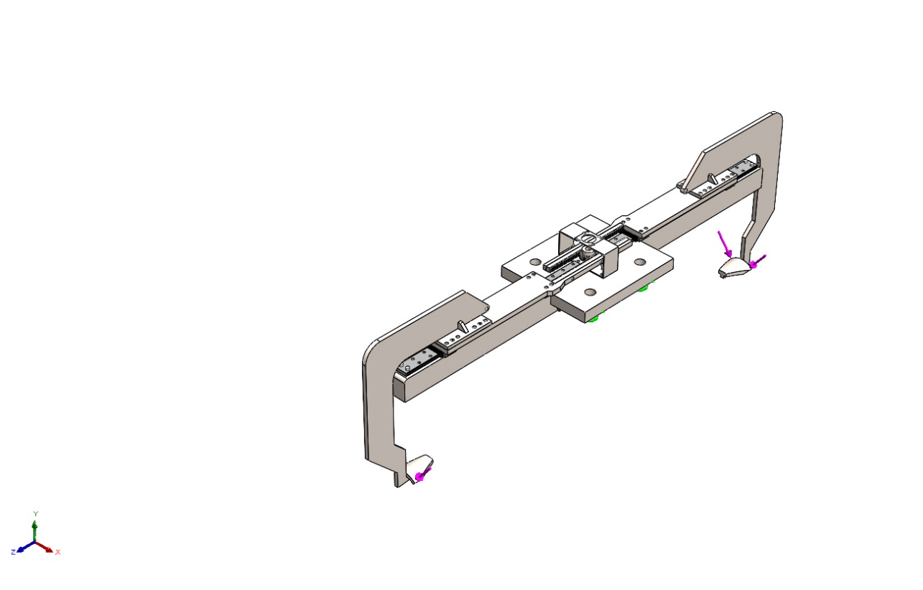
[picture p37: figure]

Model name: 100_Y-AXIS-ASSEMBLY

Current Configuration: Default

Solid Bodies
Document Name and Reference | Treated As | Volumetric Properties | Document Path/Date Modified

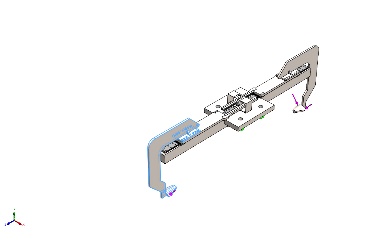
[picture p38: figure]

Cut-Extrude6 | Solid Body | Mass:8.74379 kg Volume:0.001121 m^3 Density:7,800 kg/m^3 Weight:85.6891 N | C:\Users\tatwi\Documents\GitHub\24-Increasing-Changeover-Capabilities-at-Isola\117_Y-AXIS_HOOK.SLDPRT Mar 16 12:23:02 2023

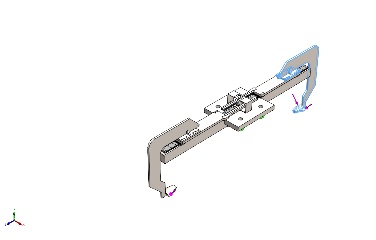
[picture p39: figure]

Cut-Extrude6 | Solid Body | Mass:8.74379 kg Volume:0.001121 m^3 Density:7,800 kg/m^3 Weight:85.6891 N | C:\Users\tatwi\Documents\GitHub\24-Increasing-Changeover-Capabilities-at-Isola\117_Y-AXIS_HOOK.SLDPRT Mar 16 12:23:02 2023

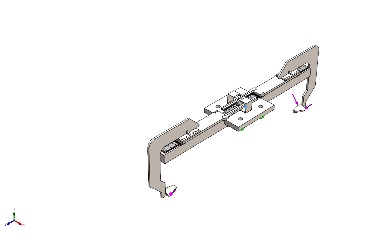
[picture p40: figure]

Revolve1 | Solid Body | Mass:0.00509185 kg Volume:6.47818e-07 m^3 Density:7,860 kg/m^3 Weight:0.0499002 N | C:\Users\tatwi\Documents\GitHub\24-Increasing-Changeover-Capabilities-at-Isola\118_Y-AXIS_BEARING.SLDPRT Mar 16 12:23:02 2023
Revolve1 | Solid Body | Mass:0.00509185 kg Volume:6.47818e-07 m^3 Density:7,860 kg/m^3 Weight:0.0499002 N | C:\Users\tatwi\Documents\GitHub\24-Increasing-Changeover-Capabilities-at-Isola\118_Y-AXIS_BEARING.SLDPRT Mar 16 12:23:02 2023
Boss-Extrude1 | Solid Body | Mass:0.00888945 kg Volume:1.13097e-06 m^3 Density:7,860 kg/m^3 Weight:0.0871166 N | C:\Users\tatwi\Documents\GitHub\24-Increasing-Changeover-Capabilities-at-Isola\119_Y-AXIS-DOWEL.SLDPRT Mar 16 12:23:02 2023
Boss-Extrude1 | Solid Body | Mass:0.00888945 kg Volume:1.13097e-06 m^3 Density:7,860 kg/m^3 Weight:0.0871166 N | C:\Users\tatwi\Documents\GitHub\24-Increasing-Changeover-Capabilities-at-Isola\119_Y-AXIS-DOWEL.SLDPRT Mar 16 12:23:02 2023
Mirror4 | Solid Body | Mass:28.91 kg Volume:0.00367811 m^3 Density:7,860 kg/m^3 Weight:283.318 N | C:\Users\tatwi\Documents\GitHub\24-Increasing-Changeover-Capabilities-at-Isola\121_Y-AXIS_BASE.SLDPRT Mar 16 12:23:02 2023

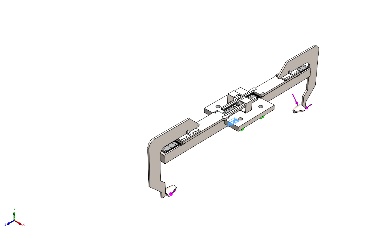
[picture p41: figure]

CBORE for M4 Hex Head Machine Screw2 | Solid Body | Mass:0.246985 kg Volume:3.1423e-05 m^3 Density:7,860 kg/m^3 Weight:2.42045 N | C:\Users\tatwi\Documents\GitHub\24-Increasing-Changeover-Capabilities-at-Isola\122-Y-AXIS_L_BRACKET.SLDPRT Mar 16 12:23:02 2023

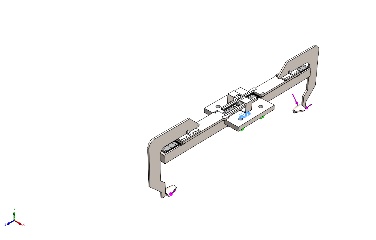
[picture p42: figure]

CBORE for M4 Hex Head Machine Screw2 | Solid Body | Mass:0.246985 kg Volume:3.1423e-05 m^3 Density:7,860 kg/m^3 Weight:2.42045 N | C:\Users\tatwi\Documents\GitHub\24-Increasing-Changeover-Capabilities-at-Isola\122-Y-AXIS_L_BRACKET.SLDPRT Mar 16 12:23:02 2023

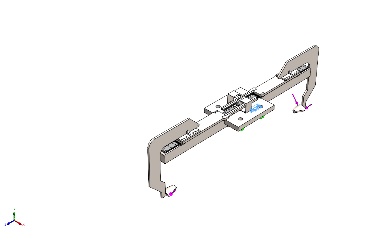
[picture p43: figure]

CBORE for M4 Hex Head Machine Screw2 | Solid Body | Mass:0.246985 kg Volume:3.1423e-05 m^3 Density:7,860 kg/m^3 Weight:2.42045 N | C:\Users\tatwi\Documents\GitHub\24-Increasing-Changeover-Capabilities-at-Isola\122-Y-AXIS_L_BRACKET.SLDPRT Mar 16 12:23:02 2023

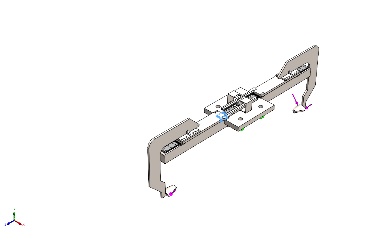
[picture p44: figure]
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

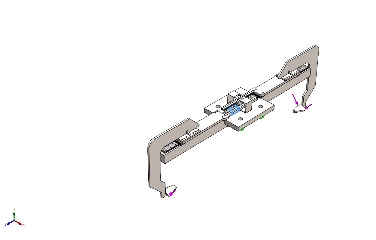
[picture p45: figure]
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

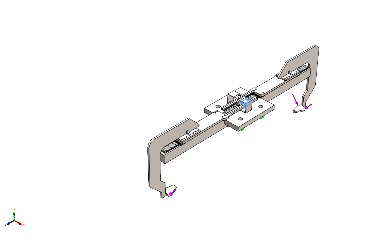
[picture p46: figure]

CBORE for M4 Hex Head Machine Screw2 | Solid Body | Mass:0.246985 kg Volume:3.1423e-05 m^3 Density:7,860 kg/m^3 Weight:2.42045 N | C:\Users\tatwi\Documents\GitHub\24-Increasing-Changeover-Capabilities-at-Isola\122-Y-AXIS_L_BRACKET.SLDPRT Mar 16 12:23:02 2023
Fillet1 | Solid Body | Mass:40.8897 kg Volume:0.00520225 m^3 Density:7,860 kg/m^3 Weight:400.719 N | C:\Users\tatwi\Documents\GitHub\24-Increasing-Changeover-Capabilities-at-Isola\123_Y-AXIS-UNDER_BASE.SLDPRT Mar 16 12:23:02 2023
SSEBWM16_b | Solid Body | Mass:0.265956 kg Volume:3.38366e-05 m^3 Density:7,860 kg/m^3 Weight:2.60637 N | C:\Users\tatwi\Documents\GitHub\24-Increasing-Changeover-Capabilities-at-Isola\131_Y_AXIS_LINEAR-RAIL_BASE.SLDPRT Mar 16 12:23:02 2023
SSEBWM16_b | Solid Body | Mass:0.265956 kg Volume:3.38366e-05 m^3 Density:7,860 kg/m^3 Weight:2.60637 N | C:\Users\tatwi\Documents\GitHub\24-Increasing-Changeover-Capabilities-at-Isola\131_Y_AXIS_LINEAR-RAIL_BASE.SLDPRT Mar 16 12:23:02 2023
SSEBWM16_b | Solid Body | Mass:0.265956 kg Volume:3.38366e-05 m^3 Density:7,860 kg/m^3 Weight:2.60637 N | C:\Users\tatwi\Documents\GitHub\24-Increasing-Changeover-Capabilities-at-Isola\131_Y_AXIS_LINEAR-RAIL_BASE.SLDPRT Mar 16 12:23:02 2023
SSEBWM16_b | Solid Body | Mass:0.265956 kg Volume:3.38366e-05 m^3 Density:7,860 kg/m^3 Weight:2.60637 N | C:\Users\tatwi\Documents\GitHub\24-Increasing-Changeover-Capabilities-at-Isola\131_Y_AXIS_LINEAR-RAIL_BASE.SLDPRT Mar 16 12:23:02 2023
SSE2BWML16G-669_r | Solid Body | Mass:1.96349 kg Volume:0.000249808 m^3 Density:7,860 kg/m^3 Weight:19.2422 N | C:\Users\tatwi\Documents\GitHub\24-Increasing-Changeover-Capabilities-at-Isola\132_Y-AXIS_LINEAR-RAIL_RAIL.SLDPRT Mar 16 12:23:02 2023
SSE2BWML16G-669_r | Solid Body | Mass:1.96349 kg Volume:0.000249808 m^3 Density:7,860 kg/m^3 Weight:19.2422 N | C:\Users\tatwi\Documents\GitHub\24-Increasing-Changeover-Capabilities-at-Isola\132_Y-AXIS_LINEAR-RAIL_RAIL.SLDPRT Mar 16 12:23:02 2023

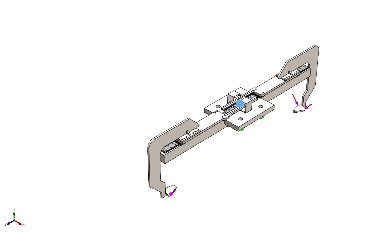
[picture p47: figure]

Cut-Extrude1 | Solid Body | Mass:0.23179 kg Volume:2.94898e-05 m^3 Density:7,860 kg/m^3 Weight:2.27154 N | C:\Users\tatwi\Documents\GitHub\24-Increasing-Changeover-Capabilities-at-Isola\141_Y-AXIS_PINION.SLDPRT Mar 16 12:23:02 2023

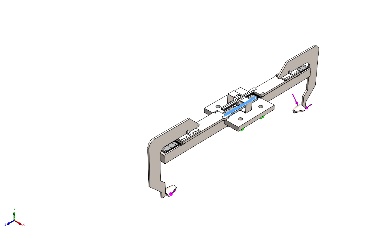
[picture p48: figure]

Fillet1 | Solid Body | Mass:0.468845 kg Volume:5.96494e-05 m^3 Density:7,860 kg/m^3 Weight:4.59468 N | C:\Users\tatwi\Documents\GitHub\24-Increasing-Changeover-Capabilities-at-Isola\142-Y-AXIS-RACK_RGEAS1_5_300_A.SLDPRT Mar 16 12:23:02 2023
Fillet1 | Solid Body | Mass:0.468845 kg Volume:5.96494e-05 m^3 Density:7,860 kg/m^3 Weight:4.59468 N | C:\Users\tatwi\Documents\GitHub\24-Increasing-Changeover-Capabilities-at-Isola\142-Y-AXIS-RACK_RGEAS1_5_300_A.SLDPRT Mar 16 12:23:02 2023

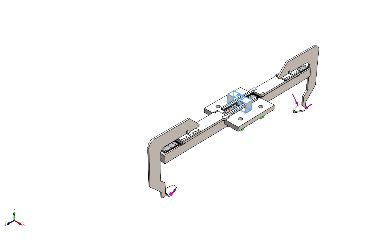
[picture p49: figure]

Cut-Extrude5 | Solid Body | Mass:0.494604 kg Volume:6.29267e-05 m^3 Density:7,860 kg/m^3 Weight:4.84712 N | C:\Users\tatwi\Documents\GitHub\24-Increasing-Changeover-Capabilities-at-Isola\143_Y-AXIS-MOTORMOUNT.SLDPRT Mar 16 12:23:02 2023

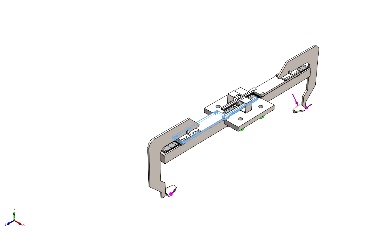
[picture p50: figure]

M4x0.7 Tapped Hole1 | Solid Body | Mass:4.713 kg Volume:0.000599618 m^3 Density:7,860 kg/m^3 Weight:46.1874 N | C:\Users\tatwi\Documents\GitHub\24-Increasing-Changeover-Capabilities-at-Isola\145_Y-AXIS_RACK-ATTACHMENT.SLDPRT Mar 16 12:23:02 2023

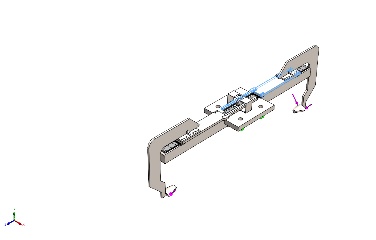
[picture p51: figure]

M4x0.7 Tapped Hole1 | Solid Body | Mass:4.713 kg Volume:0.000599618 m^3 Density:7,860 kg/m^3 Weight:46.1874 N | C:\Users\tatwi\Documents\GitHub\24-Increasing-Changeover-Capabilities-at-Isola\145_Y-AXIS_RACK-ATTACHMENT.SLDPRT Mar 16 12:23:02 2023

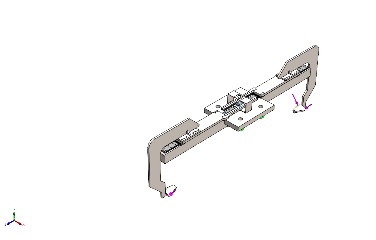
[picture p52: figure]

Boss-Extrude1 | Solid Body | Mass:0.00031752 kg Volume:4.0397e-08 m^3 Density:7,860 kg/m^3 Weight:0.0031117 N | C:\Users\tatwi\Documents\GitHub\24-Increasing-Changeover-Capabilities-at-Isola\151_Y-AXIS_FORMATE.SLDPRT Mar 16 12:46:42 2023
Revolve1 | Solid Body | Mass:0.00834988 kg Volume:1.0705e-06 m^3 Density:7,800 kg/m^3 Weight:0.0818288 N | C:\Users\tatwi\Documents\GitHub\24-Increasing-Changeover-Capabilities-at-Isola\1_1110_STOPPER.SLDPRT Mar 16 12:23:02 2023
Revolve1 | Solid Body | Mass:0.00834988 kg Volume:1.0705e-06 m^3 Density:7,800 kg/m^3 Weight:0.0818288 N | C:\Users\tatwi\Documents\GitHub\24-Increasing-Changeover-Capabilities-at-Isola\1_1110_STOPPER.SLDPRT Mar 16 12:23:02 2023
Revolve1 | Solid Body | Mass:0.00834988 kg Volume:1.0705e-06 m^3 Density:7,800 kg/m^3 Weight:0.0818288 N | C:\Users\tatwi\Documents\GitHub\24-Increasing-Changeover-Capabilities-at-Isola\1_1110_STOPPER.SLDPRT Mar 16 12:23:02 2023
Revolve1 | Solid Body | Mass:0.00834988 kg Volume:1.0705e-06 m^3 Density:7,800 kg/m^3 Weight:0.0818288 N | C:\Users\tatwi\Documents\GitHub\24-Increasing-Changeover-Capabilities-at-Isola\1_1110_STOPPER.SLDPRT Mar 16 12:23:02 2023

# Study Properties

Study name | Y-AXIS
Analysis type | Static
Mesh type | Solid Mesh
Thermal Effect: | On
Thermal option | Include temperature loads
Zero strain temperature | 298 Kelvin
Include fluid pressure effects from SOLIDWORKS Flow Simulation | Off
Solver type | Automatic
Inplane Effect: | Off
Soft Spring: | Off
Inertial Relief: | Off
Incompatible bonding options | Automatic
Large displacement | Off
Compute free body forces | On
Friction | Off
Use Adaptive Method: | Off
Result folder | SOLIDWORKS document (C:\Users\tatwi\Documents\GitHub\24-Increasing-Changeover-Capabilities-at-Isola)

# Units

Unit system: | SI (MKS)
Length/Displacement | mm
Temperature | Kelvin
Angular velocity | Rad/sec
Pressure/Stress | N/m^2

# Material Properties

| | Model Reference | Properties | Components

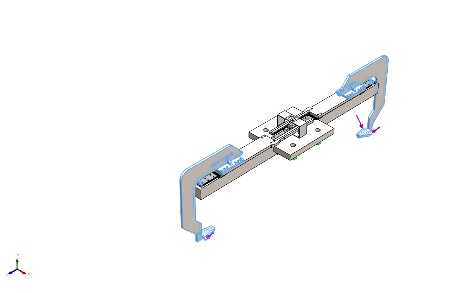
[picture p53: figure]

| | | Name: Stainless Steel (ferritic) Model type: Linear Elastic Isotropic Default failure criterion: Unknown Yield strength: 1.72339e+08 N/m^2 Tensile strength: 5.13613e+08 N/m^2 Elastic modulus: 2e+11 N/m^2 Poisson's ratio: 0.28 Mass density: 7,800 kg/m^3 Shear modulus: 7.7e+10 N/m^2 Thermal expansion coefficient: 1.1e-05 /Kelvin | SolidBody 1(Cut-Extrude6)(117_Y-AXIS_HOOK-2), SolidBody 1(Cut-Extrude6)(117_Y-AXIS_HOOK-5), SolidBody 1(Revolve1)(1_1110_STOPPER-1), SolidBody 1(Revolve1)(1_1110_STOPPER-2), SolidBody 1(Revolve1)(1_1110_STOPPER-3), SolidBody 1(Revolve1)(1_1110_STOPPER-4)

Curve Data:N/A

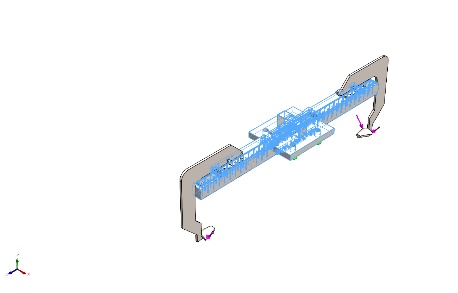
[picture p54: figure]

Name: | 201 Annealed Stainless Steel (SS)
Model type: | Linear Elastic Isotropic
Default failure criterion: | Unknown
Yield strength: | 2.92e+08 N/m^2
Tensile strength: | 6.85e+08 N/m^2
Elastic modulus: | 2.07e+11 N/m^2
Poisson's ratio: | 0.27
Mass density: | 7,860 kg/m^3
Thermal expansion coefficient: | 1.7e-05 /Kelvin

SolidBody 1(Revolve1)(118_Y-AXIS_BEARING-1),

SolidBody 1(Revolve1)(118_Y-AXIS_BEARING-2),

SolidBody 1(Boss-Extrude1)(119_Y-AXIS-DOWEL-1),

SolidBody 1(Boss-Extrude1)(119_Y-AXIS-DOWEL-2),

SolidBody 1(Mirror4)(121_Y-AXIS_BASE-1),

SolidBody 1(CBORE for M4 Hex Head Machine Screw2)(122-Y-AXIS_L_BRACKET-1),

SolidBody 1(CBORE for M4 Hex Head Machine Screw2)(122-Y-AXIS_L_BRACKET-4),

SolidBody 1(CBORE for M4 Hex Head Machine Screw2)(122-Y-AXIS_L_BRACKET-5),

SolidBody 1(CBORE for M4 Hex Head Machine Screw2)(122-Y-AXIS_L_BRACKET-6),

SolidBody 1(CBORE for M4 Hex Head Machine Screw2)(122-Y-AXIS_L_BRACKET-7),

SolidBody 1(CBORE for M4 Hex Head Machine Screw2)(122-Y-AXIS_L_BRACKET-8),

SolidBody 1(Fillet1)(123_Y-AXIS-UNDER_BASE-1),

SolidBody 1(SSEBWM16_b)(131_Y_AXIS_LINEAR-RAIL_BASE-1),

SolidBody 1(SSEBWM16_b)(131_Y_AXIS_LINEAR-RAIL_BASE-2),

SolidBody 1(SSEBWM16_b)(131_Y_AXIS_LINEAR-RAIL_BASE-3),

SolidBody 1(SSEBWM16_b)(131_Y_AXIS_LINEAR-RAIL_BASE-4),

SolidBody 1(SSE2BWML16G-669_r)(132_Y-AXIS_LINEAR-RAIL_RAIL-2),

SolidBody 1(SSE2BWML16G-669_r)(132_Y-AXIS_LINEAR-RAIL_RAIL-3),

SolidBody 1(Cut-Extrude1)(141_Y-AXIS_PINION-1),

SolidBody 1(Fillet1)(142-Y-AXIS-RACK_RGEAS1_5_300_A-1),

SolidBody 1(Fillet1)(142-Y-AXIS-RACK_RGEAS1_5_300_A-2),

SolidBody 1(Cut-Extrude5)(143_Y-AXIS-MOTORMOUNT-1),

SolidBody 1(M4x0.7 Tapped Hole1)(145_Y-AXIS_RACK-ATTACHMENT-1),

SolidBody 1(M4x0.7 Tapped Hole1)(145_Y-AXIS_RACK-ATTACHMENT-2),

SolidBody 1(Boss-Extrude1)(151_Y-AXIS_FORMATE-1)

Curve Data:N/A

# Loads and Fixtures

Fixture name | Fixture Image | Fixture Details

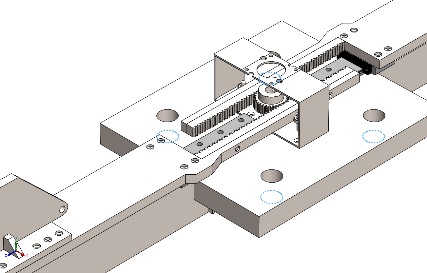
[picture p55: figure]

Fixed-1 | | Entities: 4 edge(s) Type: Fixed Geometry

Resultant Forces

Components | X | Y | Z | Resultant
Reaction force(N) | -0.135597 | 8,443.18 | 0.205688 | 8,443.18
Reaction Moment(N.m) | 0 | 0 | 0 | 0

Load name | Load Image | Load Details
Force-1 | | Entities: 2 face(s) Type: Apply normal force Value: 1,000 lbf

# Connector Definitions

No Data

# Interaction Information

Interaction | Interaction Image | Interaction Properties
Global Interaction | | Type: Bonded Components: 1 component(s) Options: Independent mesh

# Mesh information

Mesh type | Solid Mesh
Mesher Used: | Blended curvature-based mesh
Jacobian points for High quality mesh | 16 Points
Maximum element size | 52.6729 mm
Minimum element size | 2.63365 mm
Mesh Quality | High

# Sensor Details

No Data

# Resultant Forces

## Reaction forces

Selection set | Units | Sum X | Sum Y | Sum Z | Resultant
Entire Model | N | -0.135597 | 8,443.18 | 0.205688 | 8,443.18

## Reaction Moments

Selection set | Units | Sum X | Sum Y | Sum Z | Resultant
Entire Model | N.m | 0 | 0 | 0 | 0

## Free body forces

Selection set | Units | Sum X | Sum Y | Sum Z | Resultant
Entire Model | N | -158.663 | 36.4831 | -51.4591 | 170.742

## Free body moments

Selection set | Units | Sum X | Sum Y | Sum Z | Resultant
Entire Model | N.m | 0 | 0 | 0 | 1e-33

# Beams

No Data

# Study Results

Name | Type | Min | Max
Stress1 | VON: von Mises Stress | 6.131e-01N/m^2 Node: 1083992 | 3.635e+08N/m^2 Node: 1131217

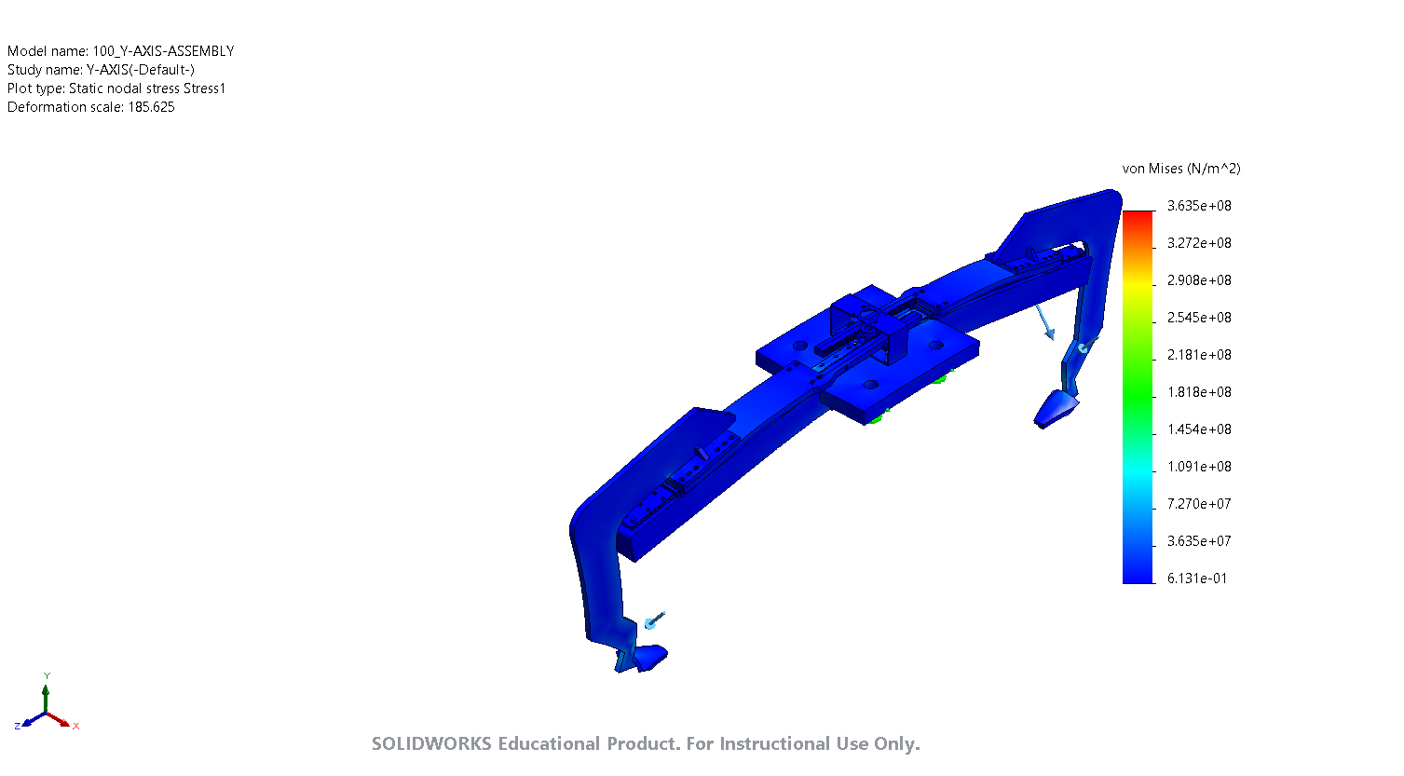
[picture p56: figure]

100_Y-AXIS-ASSEMBLY-Y-AXIS-Stress-Stress1

Name | Type | Min | Max
Displacement1 | URES: Resultant Displacement | 0.000e+00mm Node: 28170 | 8.840e-01mm Node: 38

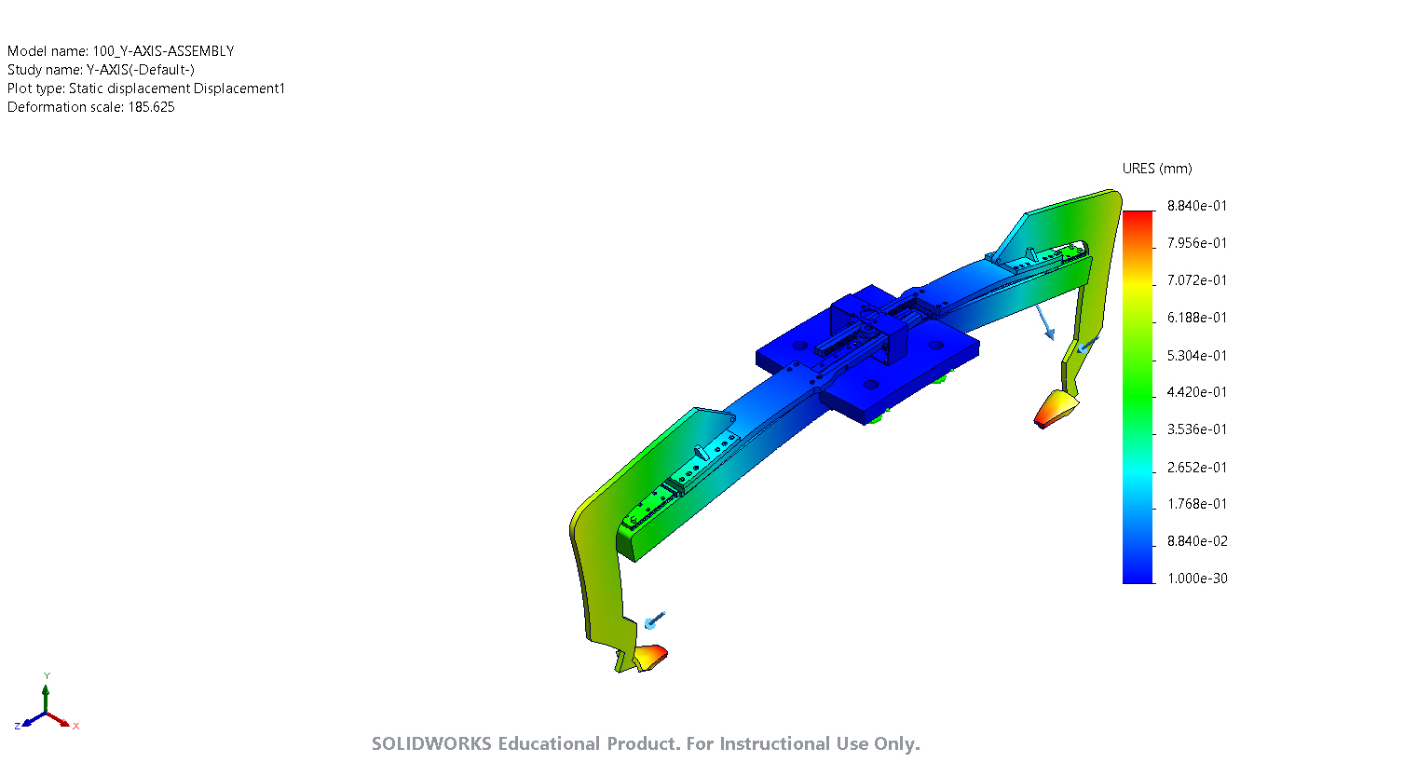
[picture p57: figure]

100_Y-AXIS-ASSEMBLY-Y-AXIS-Displacement-Displacement1

Name | Type | Min | Max
Strain1 | ESTRN: Equivalent Strain | 3.013e-12 Element: 713465 | 1.372e-03 Element: 749018

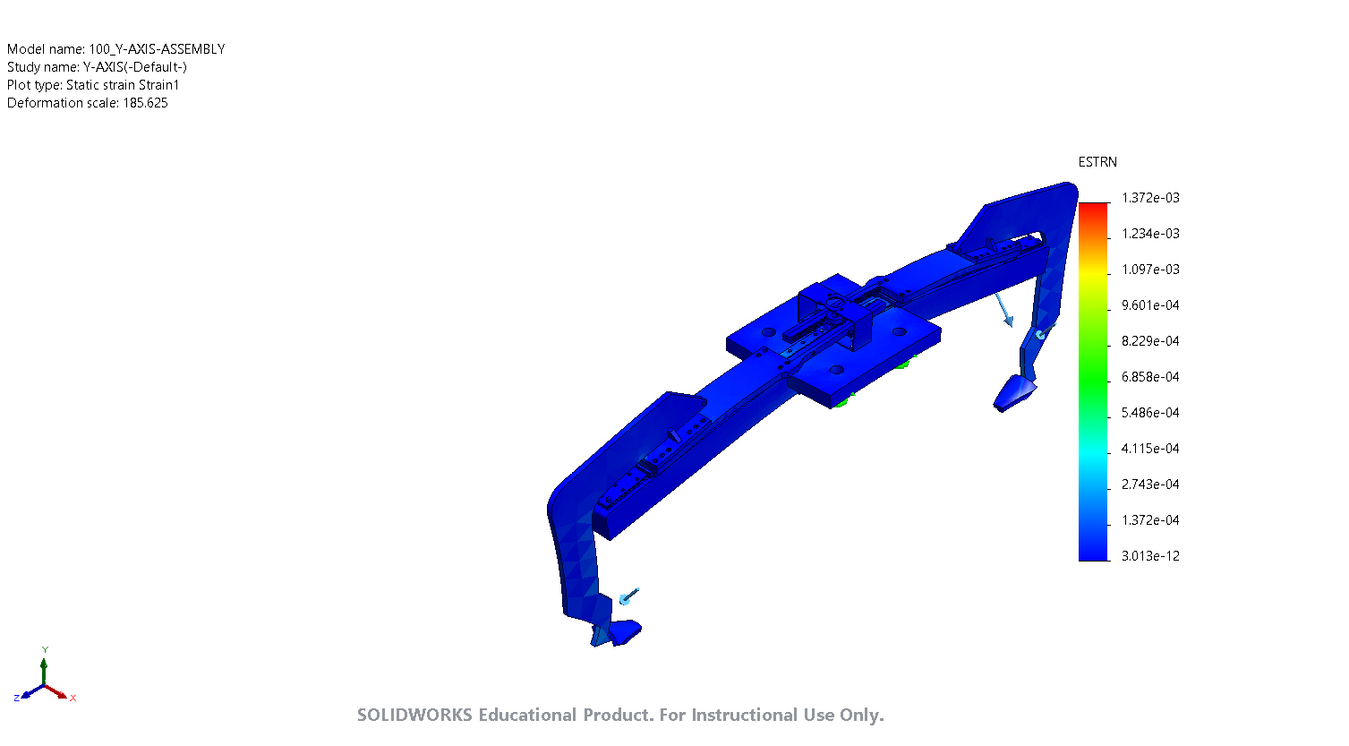
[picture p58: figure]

100_Y-AXIS-ASSEMBLY-Y-AXIS-Strain-Strain1

Name | Type | Min | Max
Factor of Safety1 | Automatic | 8.033e-01 Node: 1131217 | 4.763e+08 Node: 1083992

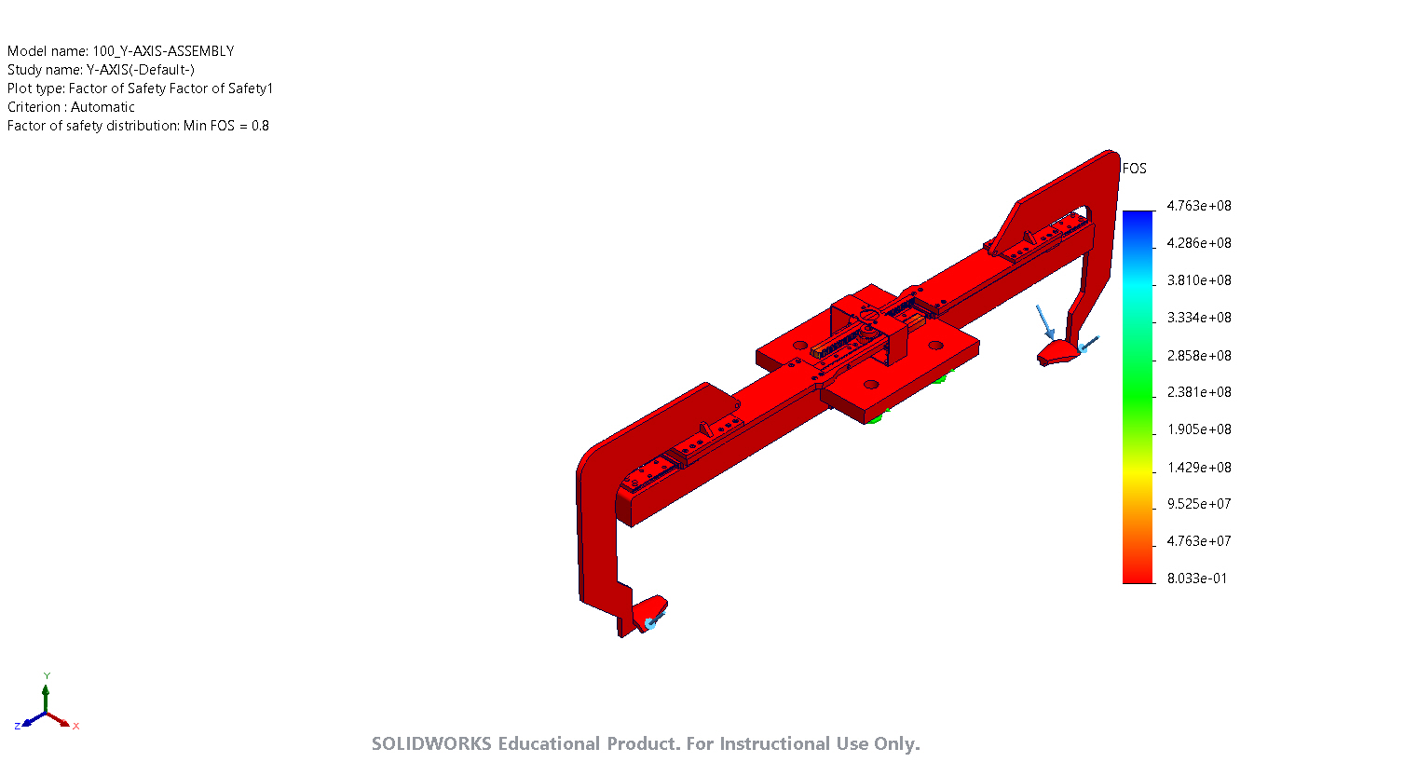
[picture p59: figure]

100_Y-AXIS-ASSEMBLY-Y-AXIS-Factor of Safety-Factor of Safety1

# Conclusion

# Appendix

Analyzed with SOLIDWORKS Simulation Simulation of 100_Y-AXIS-ASSEMBLY 16

Analyzed with SOLIDWORKS Simulation Simulation of 100_Y-AXIS-ASSEMBLY 1

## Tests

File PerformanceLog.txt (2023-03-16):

Number of Contacts: 763
Number of contact data: 60384

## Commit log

2023-01-16 DRAWING TEMPLATES
    [ASU_A-size_Sht1_Metric (2).SLDDRW]
2023-01-16 Add files via upload
    1/16/23
    1pm
    [100_Y-AXIS-ASSEMBLY.SLDASM, 117_Y-AXIS_HOOK.SLDPRT, 119_Y-AXIS-DOWEL.SLDPRT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]
2023-01-17 Add files via upload
    Might need to specify bearing path
    [1 HOOK_V2 .SLDPRT, 118_Y-AXIS_BEARING.SLDPRT]
2023-01-19 thinner grabber
    [117_Y-AXIS_HOOK.SLDPRT]
2023-03-16 Unziped x-axis
    [000_X-AXIS-ASSEMBLY.SLDASM, 001_X-AXIS-SUB_ASSEM_LINEAR_RAIL_HGW35CA1R200Z0C_Rail.SLDPRT, 002_X-AXIS_DRIVE_MAIN_PULLEY_8MX-60S-62.SLDPRT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]
2023-03-16 Revert "Unziped x-axis"
    This reverts commit eacb107b10b59c514f1abeac3d522d5145f481ab.
    [000_X-AXIS-ASSEMBLY.SLDASM, 001_X-AXIS-SUB_ASSEM_LINEAR_RAIL_HGW35CA1R200Z0C_Rail.SLDPRT, 002_X-AXIS_DRIVE_MAIN_PULLEY_8MX-60S-62.SLDPRT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]
2023-03-16 Stress Analysis for Y-AXIS
    [100_Y-AXIS-ASSEMBLY.SLDASM, 151_Y-AXIS_FORMATE.SLDPRT]
2023-03-16 Final Save 3/16/2023 for Y-Axis by Sai
    [100_Y-AXIS-ASSEMBLY.SLDASM]
2023-04-05 X-Axis Drawings
2024-06-10 Rename 210_Z-AXIS_CARRAIGE v1.zip to CAD/210_Z-AXIS_CARRAIGE v1.zip
2024-06-10 Rename ASU_A-size_Sht1_Metric (2).SLDDRW to CAD/ASU_A-size_Sht1_Metric (2).SLDDRW
    [ASU_A-size_Sht1_Metric (2).SLDDRW]
2024-06-10 Rename Asize_Sht_2 (2).slddrt to CAD/Asize_Sht_2 (2).slddrt
